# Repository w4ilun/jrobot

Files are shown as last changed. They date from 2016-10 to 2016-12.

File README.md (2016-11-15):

jrobot
A PLEN Robot Derivative designed at China . We love the PLEN2 robot but its expensive. This is our take on a lower cost version of the PLEN2 robot using 9g servo's.

The 3d printed parts are inspired by the PLEN2 parts but were redrawn from scratch to make use of the cheaper 9g servo motors.

Note: This is a work in progress. We are still busy building and testing it. Proceed at own risk :)

Please get kits [$120]
BUY KIT LINK
(https://item.taobao.com/item.htm?spm=a230r.1.14.28.0Gwvvy&id=531972040644&ns=1&abbucket=7#detail)

3d model: http://www.thingiverse.com/thing:1745439

qq group: 371582470

app: jrobot
ios(ios app store search jrobot) 
android:(http://sj.qq.com/myapp/detail.htm?apkName=jp.plen.scenography)

video demo:http://v.youku.com/v_show/id_XMTcwMTE4NjE5Mg==.html?from=y1.7-2

video app demo:https://youtu.be/BKA68jKV4QY

motion editor demo: https://youtu.be/AzxJYb-AGyE

3d printed jrobot

3d printed jrobot

3d printed jrobot

3d printed jrobot

3d printed jrobot

3d printed jrobot

3d printed jrobot

3d printed jrobot

3d printed jrobot

This software is released under the MIT License.

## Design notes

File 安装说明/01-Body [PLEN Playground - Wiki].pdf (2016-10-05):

2016/9/20 | Body [PLEN Playground Wiki]

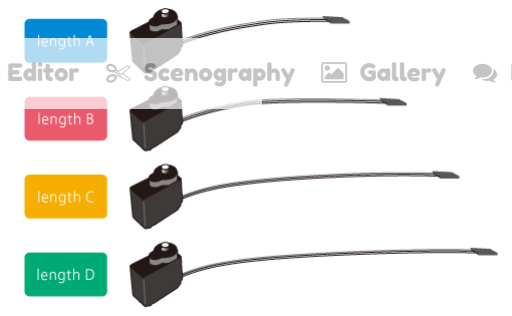
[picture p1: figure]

http://plen.jp/playground/wiki/tutorials/plen2/body | 1/3

# PLEN Playground - Wiki (http://plen.jp/playground/wiki/index.html)

# Body

## Table of Contents

1. Firmware Installation (http://plen.jp/playground/wiki/tutorials/plen2/firmware)
2. Connect a Battery (http://plen.jp/playground/wiki/tutorials/plen2/battery)
3. Arm (http://plen.jp/playground/wiki/tutorials/plen2/arm)
4. Leg (http://plen.jp/playground/wiki/tutorials/plen2/leg)
5. Head (http://plen.jp/playground/wiki/tutorials/plen2/head)
6. Body (http://plen.jp/playground/wiki/tutorials/plen2/body) Current section
7. Merge the Parts (http://plen.jp/playground/wiki/tutorials/plen2/merge)
8. Attach Covers (http://plen.jp/playground/wiki/tutorials/plen2/cover)
9. Tuning Up Home Positions (http://plen.jp/playground/wiki/tutorials/plen2/tune)

Prev < Head (http://plen.jp/playground/wiki/tutorials/plen2/head)
Next > Merge the Parts (http://plen.jp/playground/wiki/tutorials/plen2/merge)

## Parts List

Parts list of the body is enumerated below.

Name | Q'ty
body_middle.stl [https://github.com/plenprojectcompany/PLEN2/blob/master/stl/body_middle.stl] | 1
servo_bracket.stl [https://github.com/plenprojectcompany/PLEN2/blob/master/stl/servo_bracket.stl] | 2
servo_bracket_mirror.stl [https://github.com/plenprojectcompany/PLEN2/blob/master/stl/servo_bracket_mirror.stl] | 2
servo_fixer.stl [https://github.com/plenprojectcompany/PLEN2/blob/master/stl/servo_fixer.stl] | 1
Servo Motor (Length A) | 2
Servo Motor (Length B) | 2
Low Head Screw | 4
Screw | 2
Finished Head (http://plen.jp/playground/wiki/tutorials/plen2/head) | 1
Control Board with Power Supply (http://plen.jp/playground/wiki/tutorials/plen2/battery) | 1

## Print Detail

Body (http://plen.jp/playground/wiki/specifications/print_detail/body)

## Assembling Process

### Parts List

### Attach Servos

- Home (http://plen.jp/playground/) Motion Editor (http://plen.jp/playground/motion-editor/) Scenography (http://plen.jp/playground/scenography/) Gallery (http://plen.jp/playground/gallery/) Forum (http://plen.jp/playground/forum/) Wiki (http://plen.jp/playground/wiki/)

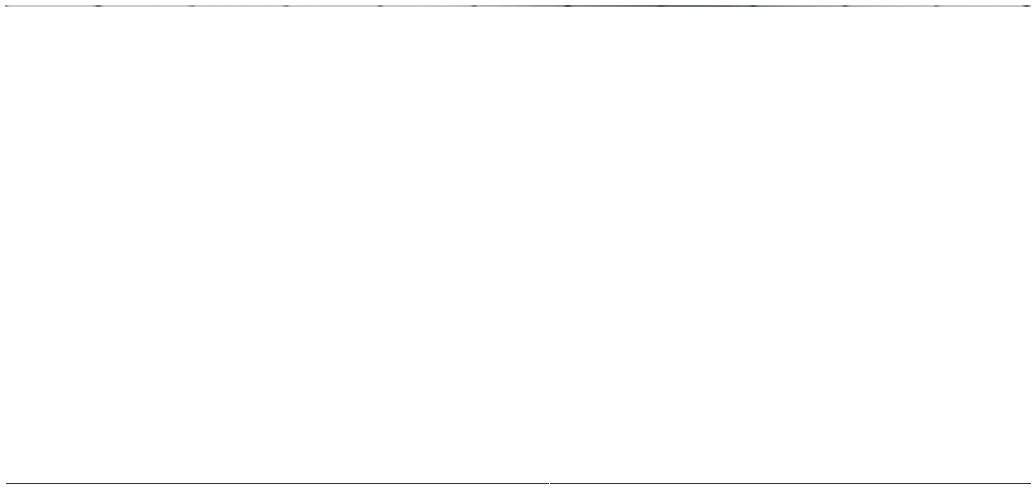
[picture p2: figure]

Attention!: Servos' cables are passed through inside the body's gap.

### Attach the Finished Head

Attention!: Head-board's cable is passed through inside the body's gap.

### Attach Spacer for Servos

### Attach the Control Board

Attention!: Control-board's cable is passed through inside the body's gap.

Attention!: Please use normal screws to attach the control-board.

### Attach the Brackets

Attention!: Before to attach the brackets, you should connect servos' cables and the control-board. When it was completed, please turn on both switches and keep the status.

Attention!: Please connect the white wire which is owned by a servo to inside of the control-board.

Attention!: Attach a servo-bracket to the body. At that time, please check it is placed approximately parallel to edge of the body.

Attention!: Attach a servo-bracket (mirror) to the body. At that time, please check it is placed approximately parallel to edge of the body.

Attention!: Attach a servo-bracket to the body. At that time, please check it is placed approximately parallel to edge of the body.

Attention!: Attach a servo-bracket (mirror) to the body. At that time, please check it is placed approximately parallel to edge of the body.

### Finished Body

Prev < Head (http://plen.jp/playground/wiki/tutorials/plen2/head)
Next > Merge the Parts (http://plen.jp/playground/wiki/tutorials/plen2/merge)

tutorials/plen2/body.txt · Last modified: 2016/04/21 19:39 (external edit)

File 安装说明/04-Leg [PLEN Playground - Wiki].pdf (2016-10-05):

2016/9/20 | Leg [PLEN Playground Wiki]

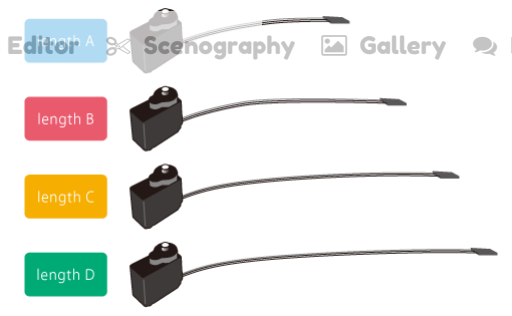
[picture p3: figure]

http://plen.jp/playground/wiki/tutorials/plen2/leg | 1/6

# PLEN Playground - Wiki (http://plen.jp/playground/wiki/index.html)

# Leg

## Table of Contents

1. Firmware Installation (http://plen.jp/playground/wiki/tutorials/plen2/firmware)
2. Connect a Battery (http://plen.jp/playground/wiki/tutorials/plen2/battery)
3. Arm (http://plen.jp/playground/wiki/tutorials/plen2/arm)
4. Leg (http://plen.jp/playground/wiki/tutorials/plen2/leg) Current section
5. Head (http://plen.jp/playground/wiki/tutorials/plen2/head)
6. Body (http://plen.jp/playground/wiki/tutorials/plen2/body)
7. Merge the Parts (http://plen.jp/playground/wiki/tutorials/plen2/merge)
8. Attach Covers (http://plen.jp/playground/wiki/tutorials/plen2/cover)
9. Tuning Up Home Positions (http://plen.jp/playground/wiki/tutorials/plen2/tune)

Prev < Arm (http://plen.jp/playground/wiki/tutorials/plen2/arm)
Next > Head (http://plen.jp/playground/wiki/tutorials/plen2/head)

## Parts List

Parts list of the left leg is enumerated below. If you would like to assemble the right leg, please use parts which have '_mirror' suffix or no suffix.

Name | Q'ty
serve_horn.stl [https://github.com/plenprojectcompany/PLEN2/blob/master/stl/servo_horn.stl] | 4
servo_assem_type2.stl [https://github.com/plenprojectcompany/PLEN2/blob/master/stl/servo_assem_type2.stl] | 1
servo_assem_type2_mirror.stl [https://github.com/plenprojectcompany/PLEN2/blob/master/stl/servo_assem_type2_mirror.stl] | 1
servo_bracket_knee_mirror.stl [https://github.com/plenprojectcompany/PLEN2/blob/master/stl/servo_bracket_knee_mirror.stl] | 1
servo_bracket_shin_mirror.stl [https://github.com/plenprojectcompany/PLEN2/blob/master/stl/servo_bracket_shin_mirror.stl] | 1
servo_bracket_ankle_1_mirror.stl [https://github.com/plenprojectcompany/PLEN2/blob/master/stl/servo_bracket_ankle_1_mirror.stl] | 1
servo_bracket_ankle_2_mirror.stl [https://github.com/plenprojectcompany/PLEN2/blob/master/stl/servo_bracket_ankle_2_mirror.stl] | 1
foot_mirror.stl [https://github.com/plenprojectcompany/PLEN2/blob/master/stl/foot_mirror.stl] | 1
Servo Motor (Length B) | 2
Servo Motor (Length C) | 1
Servo Motor (Length D) | 2

## Print Detail

Leg x2 (http://plen.jp/playground/wiki/specifications/print_detail/legs)

## Assembling Process

### Parts List

- Home Motion Editor Scenography Gallery (http://plen.jp/playground/wiki/_media/tutorials/plen2/motors.png) Forum (http://plen.jp/playground/forum/) Wiki (http://plen.jp/playground/wiki/_media/tutorials/plen2/motors.png)

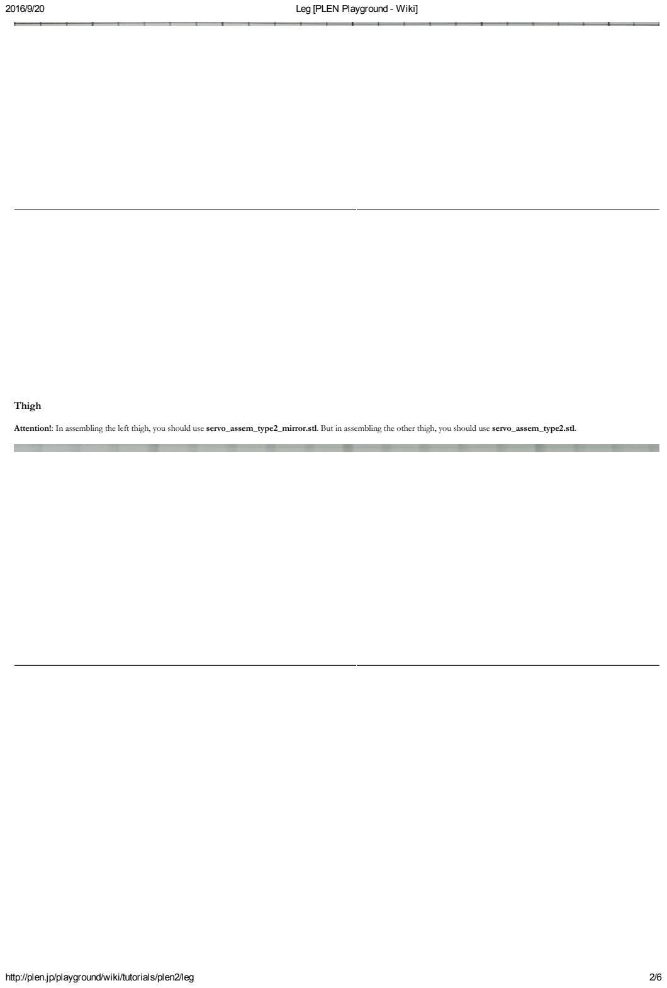
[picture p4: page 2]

### Thigh

Attention!: In assembling the left thigh, you should use servo_assem_type2_mirror.stl. But in assembling the other thigh, you should use servo_assem_type2.stl.

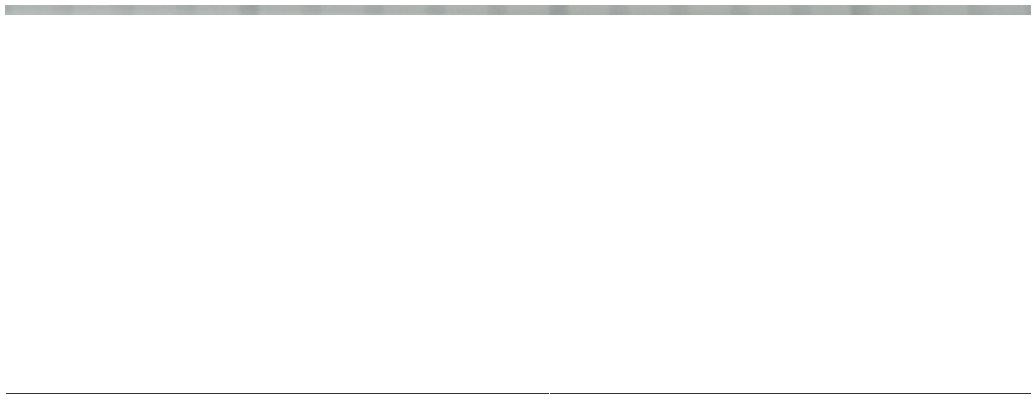
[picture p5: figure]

### Knee

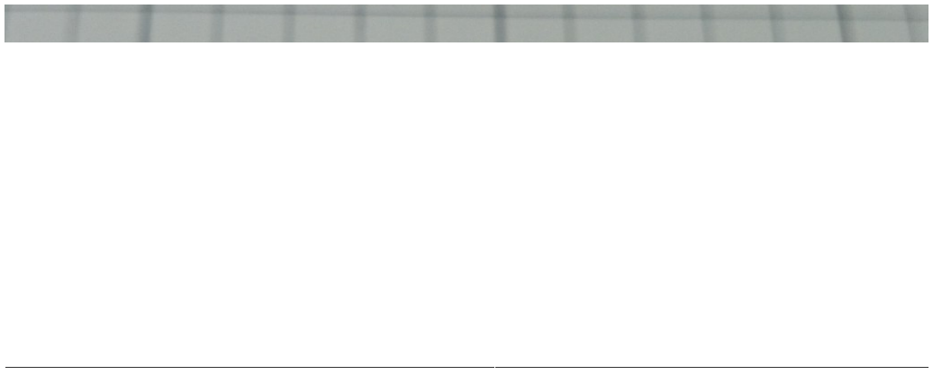
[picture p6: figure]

### Upper Foot

Attention!: In assembling the left upper foot, you should use servo_assem_type2.stl. But in assembling the other upper foot, you should use servo_assem_type2_mirror.stl.

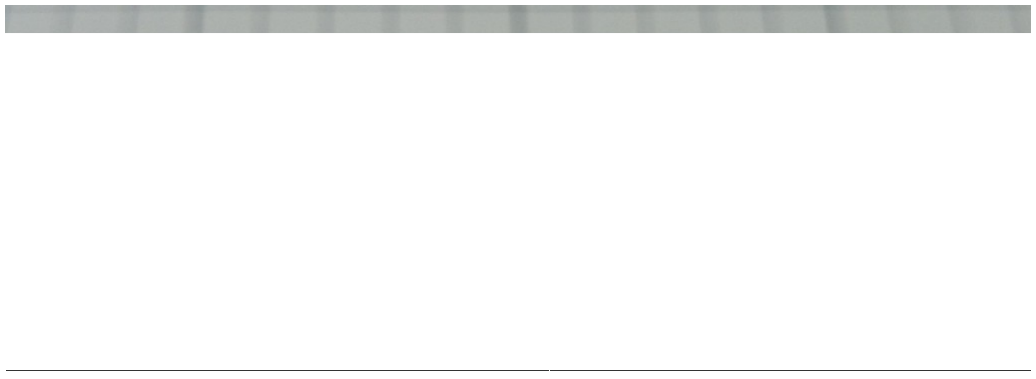
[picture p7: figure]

### Lower Foot

Attention!: If you assemble plastic cast parts, this step has already been completed.

### Merge Parts

Attention!: Before to merge the parts, you should connect servos' cables and the control-board. When it was completed, please turn on both switches and keep the status.

Attention!: Please connect the white wire which is owned by a servo to inside of the control-board.

Attention!: Attach a servo-horn to the left thigh. At that time, please check it is placed approximately parallel to edge of the servo.

Attention!: Attach a servo-horn to the left knee. At that time, please check it is placed approximately parallel to edge of the servo.

Attention!: Attach a servo-horn to the left upper foot. At that time, please check it is placed approximately parallel to edge of the servo.

Attention!: In merging the left shin and the left upper foot, servos' cables are passed through inside the left shin.

Attention!: Attach a servo-horn to the left upper foot. At that time, please check it is placed approximately parallel to edge of the servo.

### Finished Leg

Prev < Arm (http://plen.jp/playground/wiki/tutorials/plen2/arm)
Next > Head (http://plen.jp/playground/wiki/tutorials/plen2/head)

tutorials/plen2/leg.txt · Last modified: 2016/04/21 19:38 (external edit)

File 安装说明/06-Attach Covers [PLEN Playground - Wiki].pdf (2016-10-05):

2016/9/20 | Attach Covers [PLEN Playground Wiki]
http://plen.jp/playground/wiki/tutorials/plen2/cover | 1/7

## PLEN Playground - Wiki (http://plen.jp/playground/wiki/index.html)

# Attach Covers

## Table of Contents

1. Firmware Installation (http://plen.jp/playground/wiki/tutorials/plen2/firmware)
2. Connect a Battery (http://plen.jp/playground/wiki/tutorials/plen2/battery)
3. Arm (http://plen.jp/playground/wiki/tutorials/plen2/arm)
4. Leg (http://plen.jp/playground/wiki/tutorials/plen2/leg)
5. Head (http://plen.jp/playground/wiki/tutorials/plen2/head)
6. Body (http://plen.jp/playground/wiki/tutorials/plen2/body)
7. Merge the Parts (http://plen.jp/playground/wiki/tutorials/plen2/merge)
8. Attach Covers (http://plen.jp/playground/wiki/tutorials/plen2/cover) Current section
9. Tuning Up Home Positions (http://plen.jp/playground/wiki/tutorials/plen2/tune)

Prev < Merge the Parts (http://plen.jp/playground/wiki/tutorials/plen2/merge)
Next > Tuning Up Home Positions (http://plen.jp/playground/wiki/tutorials/plen2/tune)

## Parts List

Parts list of the covers is enumerated below.

Name | Q'ty
body_front.stl [https://github.com/plenprojectcompany/PLEN2/blob/master/stl/body_front.stl] | 1
body_rear.stl [https://github.com/plenprojectcompany/PLEN2/blob/master/stl/body_rear.stl] | 1
power_switch_holder.stl [https://github.com/plenprojectcompany/PLEN2/blob/master/stl/power_switch_holder.stl] | 1
Finished To Merge PLEN2 (http://plen.jp/playground/wiki/tutorials/plen2/merge) | 1

## Print Detail

Body (http://plen.jp/playground/wiki/specifications/print_detail/body)

## Assembling Process

Parts List

- Home (http://plen.jp/playground/) Motion Editor (http://plen.jp/playground/motion-editor/) Scenography (http://plen.jp/playground/scenography/) Gallery (http://plen.jp/playground/gallery/) Forum (http://plen.jp/playground/forum/) Wiki (http://plen.jp/playground/wiki/)

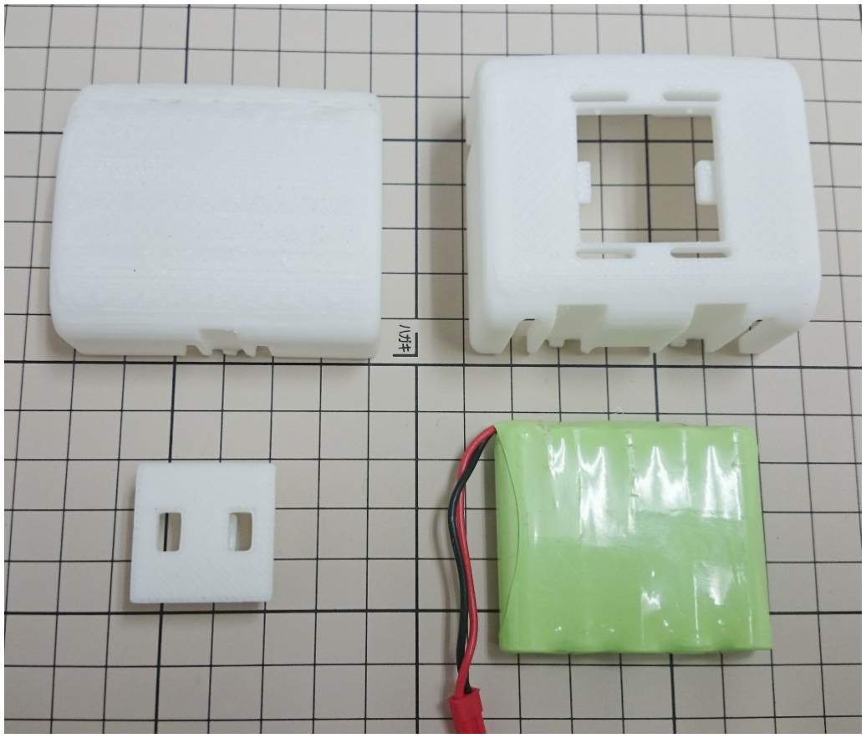
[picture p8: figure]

Attach Switch Holder

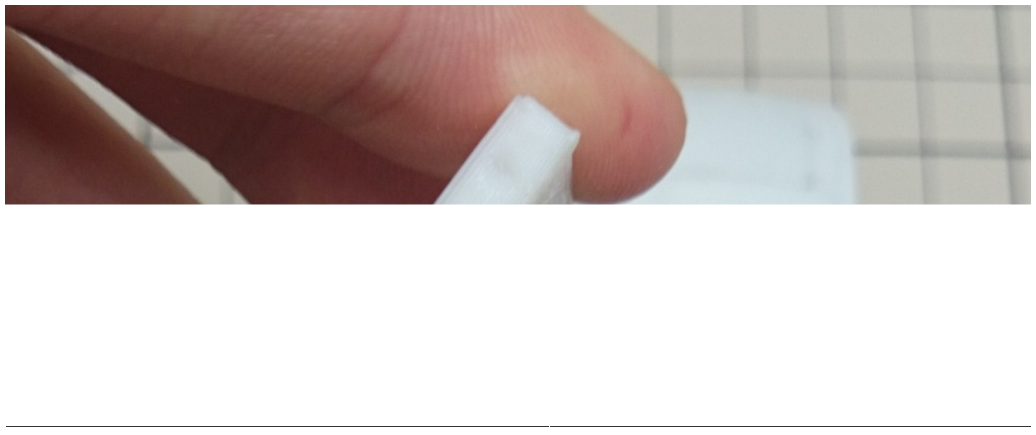
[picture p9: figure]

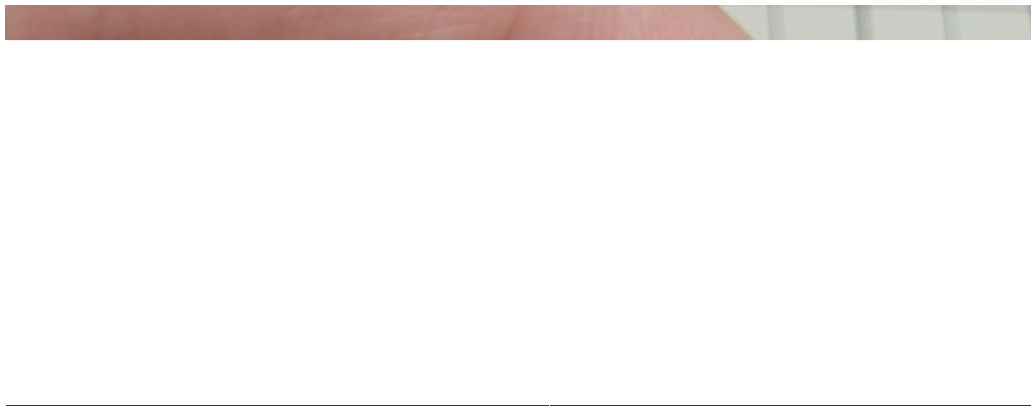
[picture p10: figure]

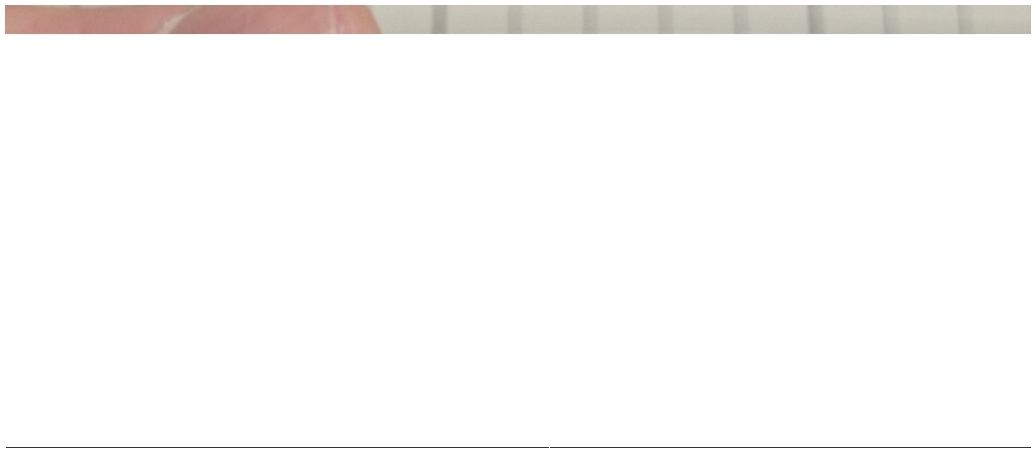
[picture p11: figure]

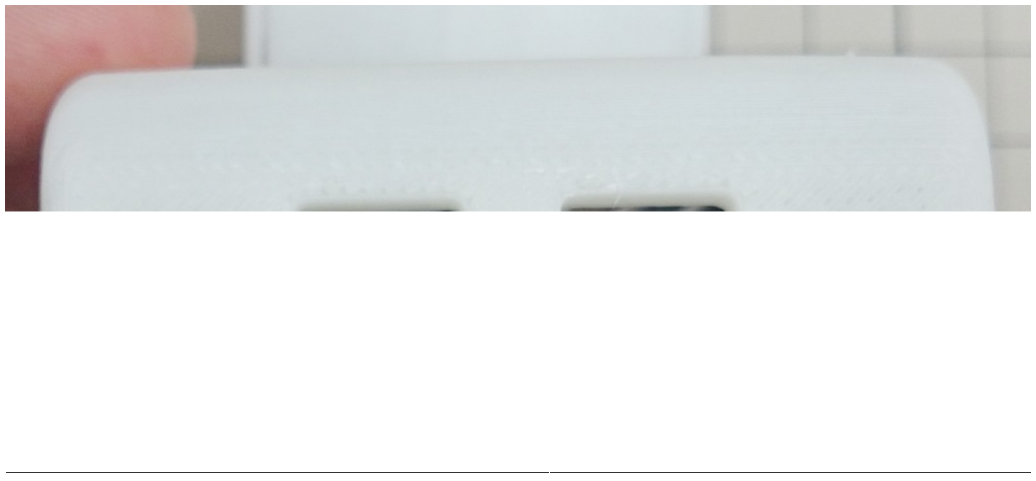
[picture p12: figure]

Attach Back Cover

Attention!: Please bundle servos' cables and fit the gap on the back.

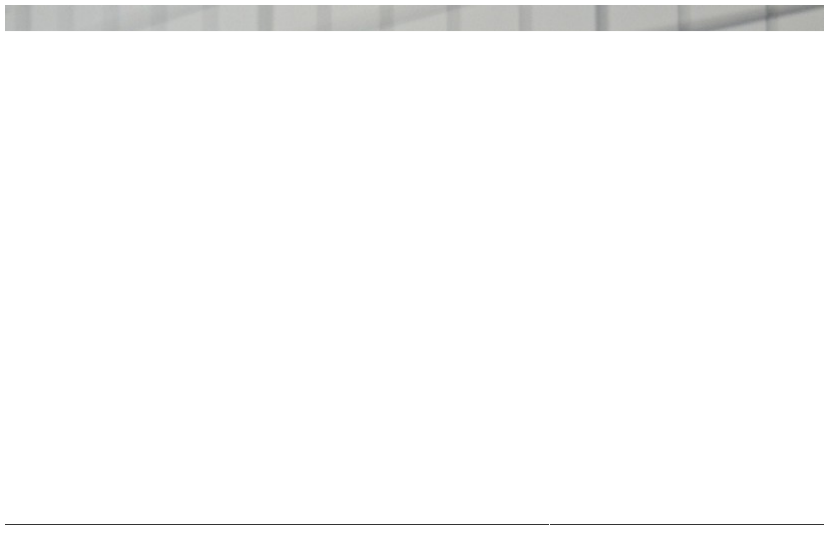
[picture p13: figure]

Attach Chest Cover

Attention!: Please fit the battery's cables gap inside the chest.

Finished PLEN2

Prev < Merge the Parts (http://plen.jp/playground/wiki/tutorials/plen2/merge)
Next > Tuning Up Home Positions (http://plen.jp/playground/wiki/tutorials/plen2/tune)

tutorials/plen2/cover.txt · Last modified: 2016/04/21 19:39 (external edit)

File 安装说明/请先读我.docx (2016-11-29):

1. 注意点：
    i. 关于电池：出厂锂电处于不饱和状态(不知道有多少电)，请先给电池充满电(充电器灯的状态会从红色->橙色->绿色，绿色时表示电池已经完全充满),电池接到电池连接线的时候，请务必保证红色线对红色线，黑色线对黑色线,每个电池有两组线(一组用来充电，一组用来放电，随意选一组，这样是为了可以不用拆plen2前胸就能充电)
    ii. 在使用机器人的过程中，如果发现机器人的眼睛灭了，即表示电池电量即将不足，请及时充电。
  b) 关于app：可以在IOS应用市场或在Android二个应用市场 (应用宝| 豌豆荚)搜索jrobot下载。请阅读app左侧菜单栏的帮助和反馈，了解如何配置网络和连接机器人。
  c) 关于app中的网络配置：
    i. 一键配置到室内wifi：

请在配置前先关闭Robot电源，然后再SSID和密码端填入家里使用的路由器的SSID和密码(务必确保这两项正确，否则配置会失败)，然后打开Robot电源，此时要立刻点击APP中的配置按钮,等待30秒左右，Android客户端会返回配置结果，IOS的暂时无返回结果的对话框，可以手动点击退出配置，然后进入设备扫描页面扫描机器人，若配置成功此处能扫描到机器人。

    ii. 无wifi情况下

打开机器人电源，等待30秒后，Robot会退出接受网络配置状态，进入创建自主热点模式，此时可以使用手机在Wifi界面搜索Robot的热点( SSID:Jrobot*****,密码为12345678xyz)，接着在扫描设备界面扫描到机器人并连接后就可以用APP控制Robot了。

  d) 关于舵机回中，PLEN2的仿人形结构和舵机的转动角度范围(<180度)限制每个舵机的初始角度不能是90度，而且每个关节的初始角度不一定一样，切记切记！！！

所以在安装关节的时候，请务必如下操作：

1.关闭主板电源

2.先把舵机插到主板上对应这个关节的舵机插槽

3.打开主板电源，舵机自动转到对应关节的初始位置。

4.关闭主板电源，安装关节。

5.打开主板电源，连上APP，在APP中的开发者模式->回中，将对应的关节微调，调正，然后点回中界面左侧的回中将调整后的回中角度保存到Robot

e) 关于舵机及摆臂和轴承的处理：

1.每个舵机的两个耳朵都需要剪去，尽量剪平，另外把舵机上的贴纸都撕去

2.小轴承用于虚轴处，固定在打印件上，塞进去后，压平即可。

3.舵机摆臂用到了2中，一种是半一字的摆臂，用在腿各个关节和手关节，只需要将摆臂末端稍微剪短后放入打印件用胶水固定(也可以关节安装完后再用胶水稍微固定下，前者刚性好，难安装，后者好安装，刚性略差);另外一种摆臂是圆形，用在肩关节和大腿根关节，用胶水固定后，重物压着，牢固后即可以安装。

f) 关于板子：

1.主板固件已经刷好，动作文件均已经下载好，直接用即可(除非要对固件进行修改，并且对这一块很熟悉，否则不推荐自己更新固件)

2.头板和主板的3pin的连接线可以通过把接插件竖直的方式放入头部(横着放不进)

2. 关于安装，

1.安装顺序，先胸部四个舵机，电池，头，头板，主板，双手并安装到身体上(及时对手部以及大腿根舵机进行微调进入双手自然放下的立正姿势)，双腿(及时对腿部舵机进行微调进入双手自然放下的立正姿势)，双腿安装到身体上

2.可以看该目录下各部位的安装说明pdf，也可以参照plen2官网的安装说明(本套3D模型是在PLEN2的模型上进行了修改，主要是解决舵机摆臂的问题，无需使用官方的注塑件，只需要使用舵机自己带的摆臂即可，其余安装方式和原版一致)http://plen.jp/playground/wiki/tutorials/index.html

3. 接线图(如果看不清楚标号，可以看同级目录下的接线图.png,因为做了一些升级，舵机的接线序号和原版的有些差别，以本图为准，另外无需看主板上的丝印)：

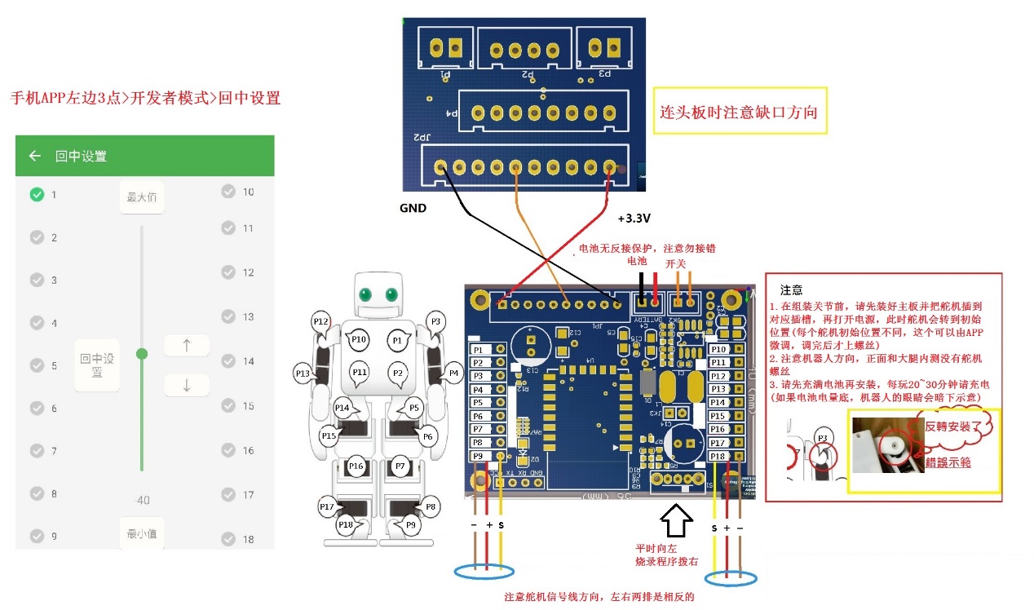
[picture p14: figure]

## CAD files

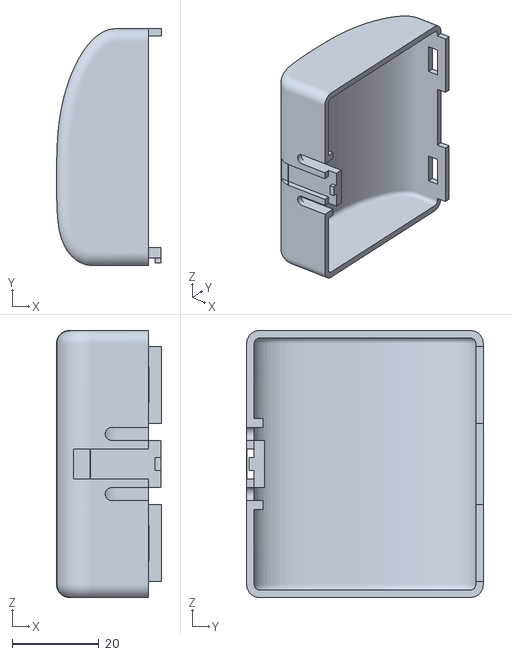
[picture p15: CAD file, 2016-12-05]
stl/body/body_front.STL
24.2 x 54.6 x 61.6

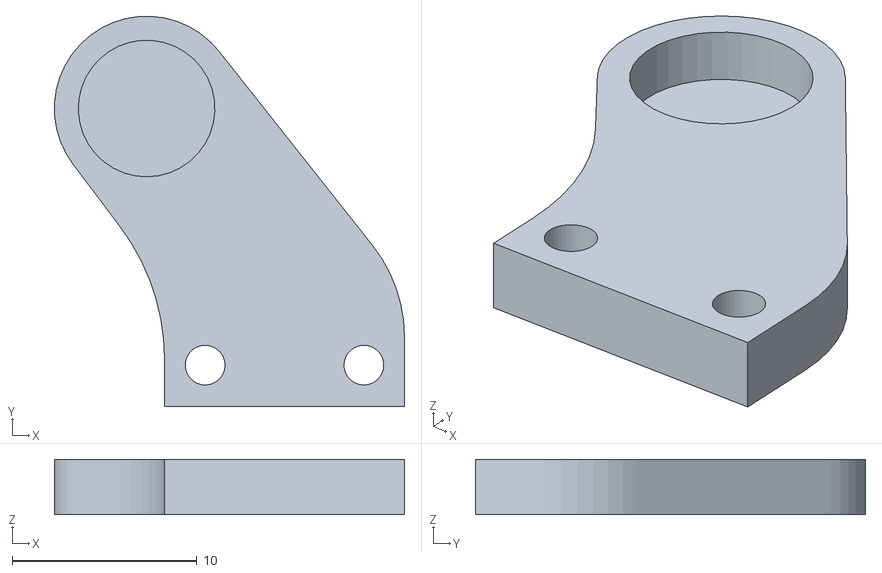
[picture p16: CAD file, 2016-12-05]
stl/body/servo_type/servo_bracket_part1_mirror.STL
19.0 x 21.1 x 3.00

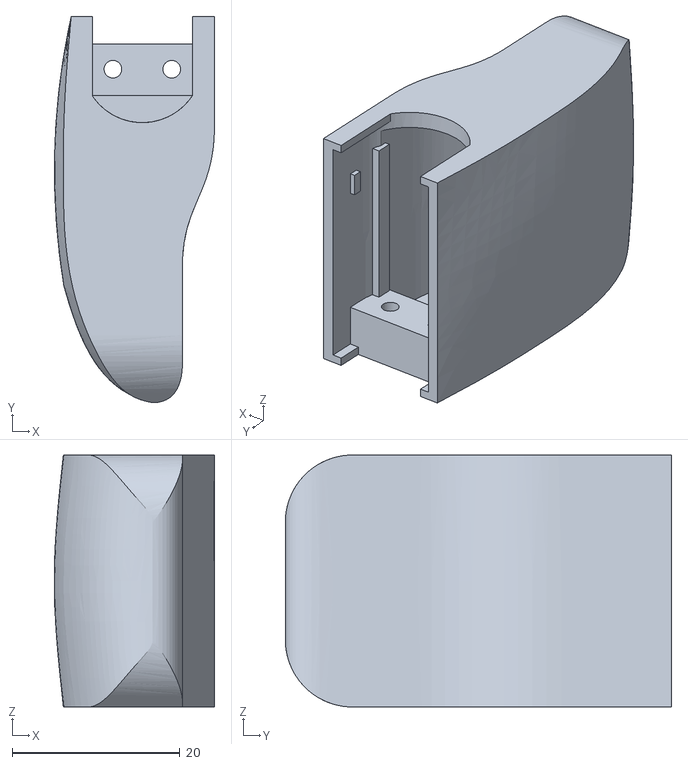
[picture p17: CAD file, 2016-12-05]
stl/hand/hand_mirror.STL
19.1 x 46.0 x 30.0

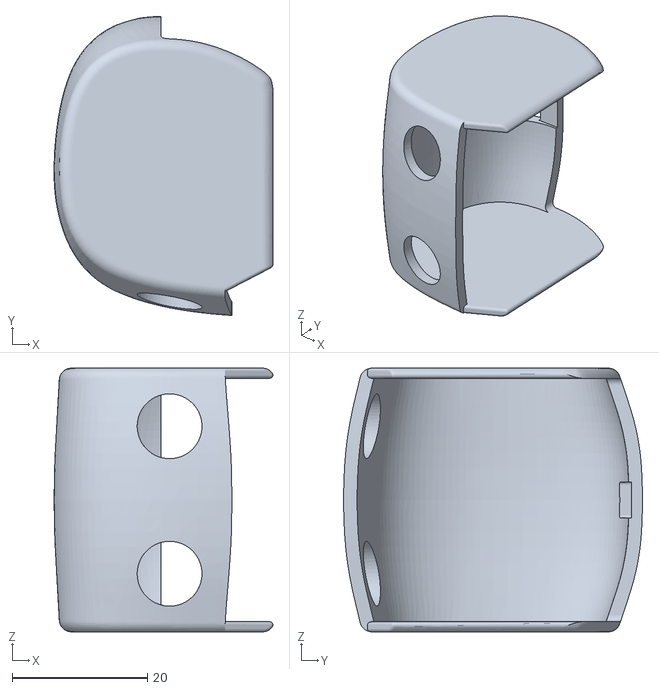
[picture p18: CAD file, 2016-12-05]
stl/head/HEAD.STL
32.4 x 44.3 x 39.0

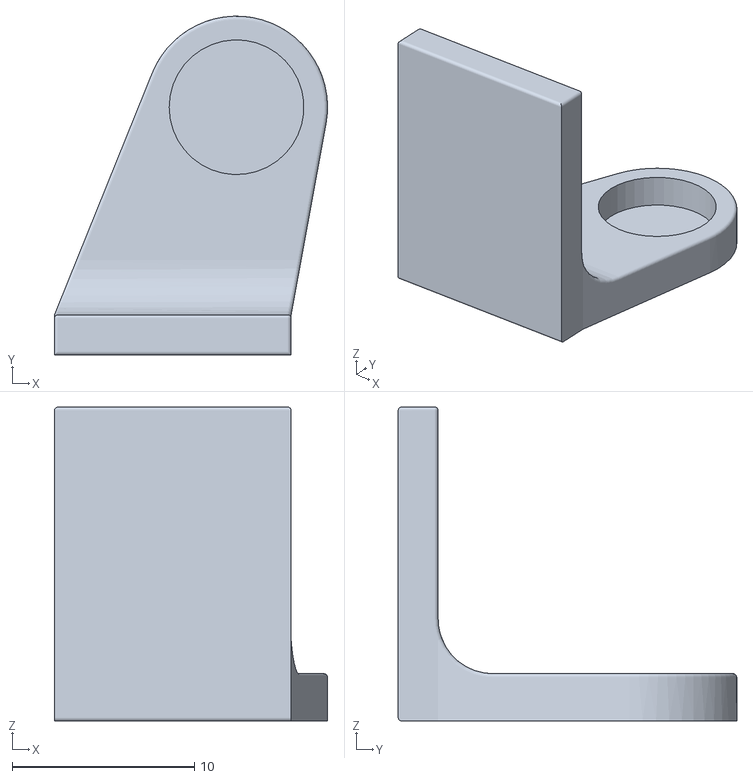
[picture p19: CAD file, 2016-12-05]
stl/leg/foot/servo_bracket_ankle_2_mirror.STL
15.0 x 18.6 x 17.2

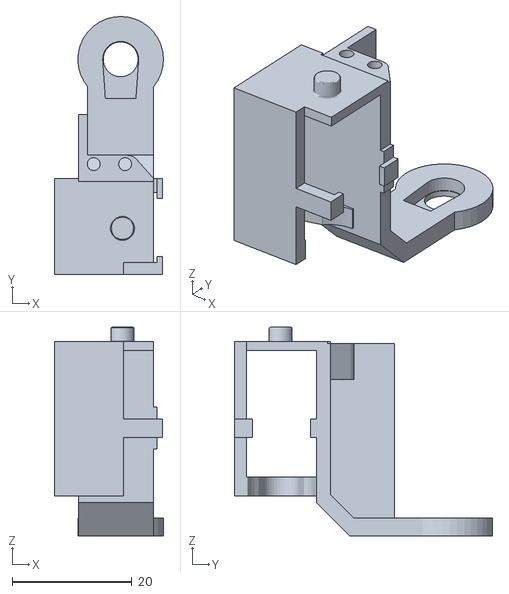
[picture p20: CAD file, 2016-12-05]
stl/leg/knee/servo_bracket_knee.STL
18.2 x 43.0 x 34.8

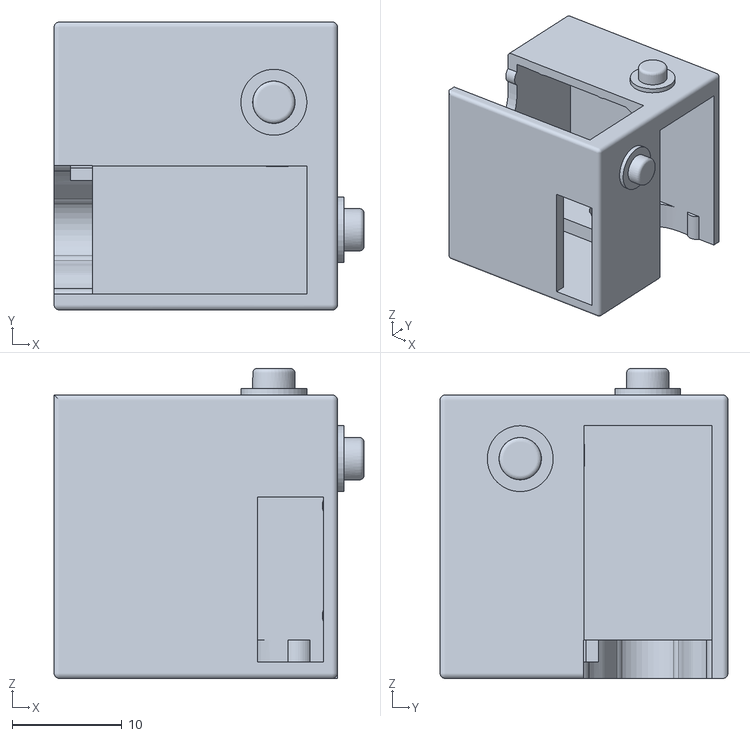
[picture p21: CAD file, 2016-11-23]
stl/leg/servo_assem_type2.STL
28.2 x 26.2 x 28.2

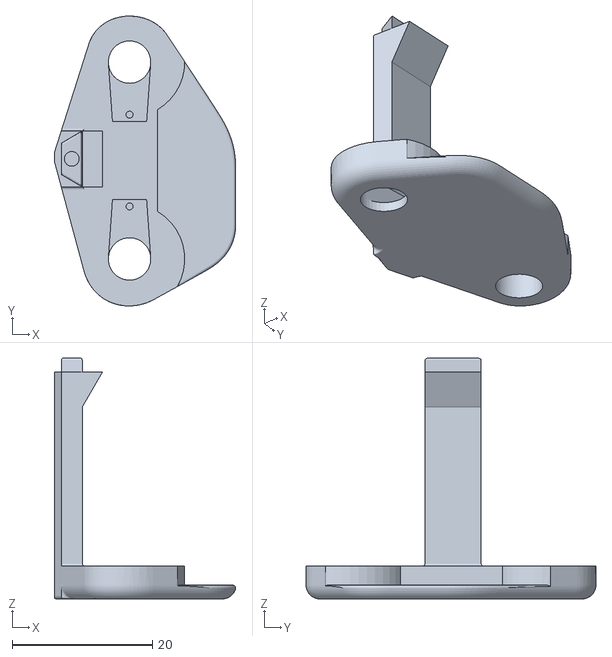
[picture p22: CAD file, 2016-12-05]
stl/leg/shin/servo_bracket_shin_part1.STL
25.9 x 41.4 x 34.4

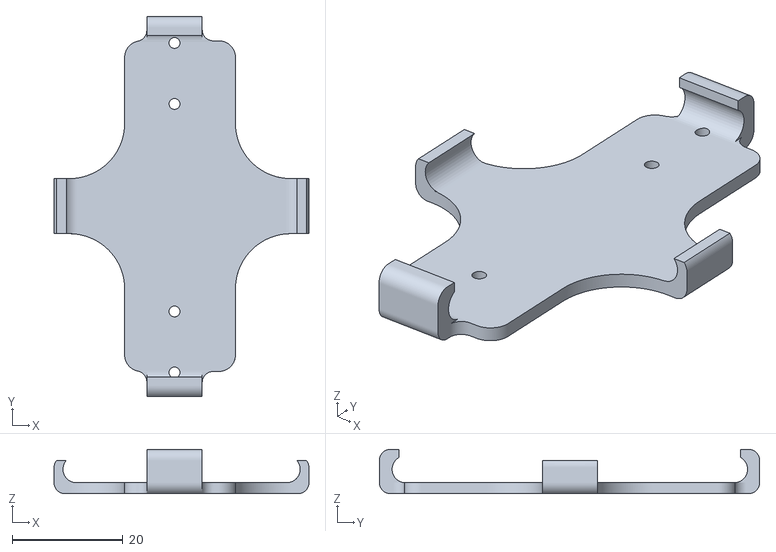
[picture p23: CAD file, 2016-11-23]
stl/toys/skate_base.stl
46.0 x 68.6 x 8.00

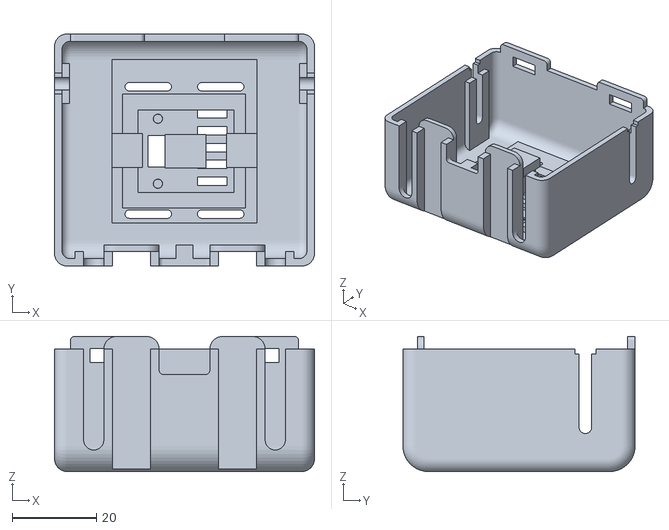
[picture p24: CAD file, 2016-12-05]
stl/body/body_rear_op.STL
61.6 x 55.0 x 32.0

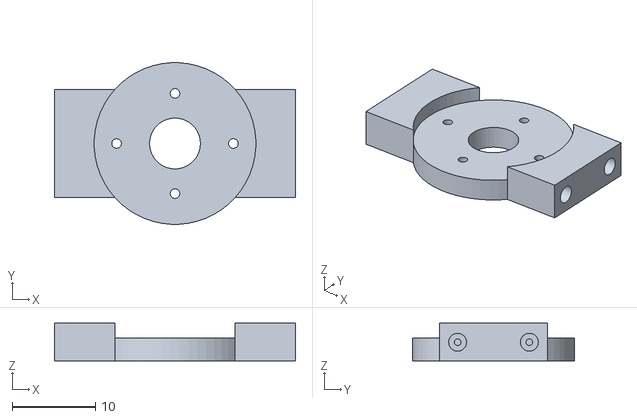
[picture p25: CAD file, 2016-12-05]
stl/body/servo_type/servo_bracket_part2.STL
28.9 x 19.4 x 4.55

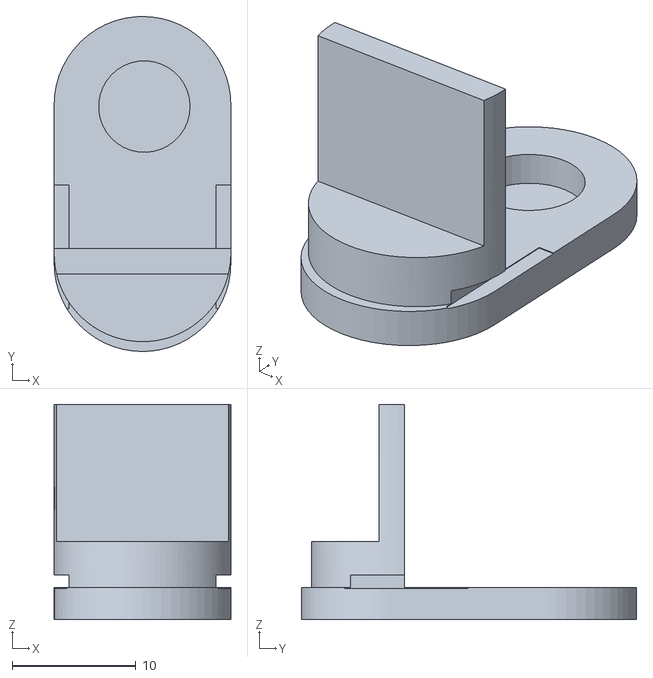
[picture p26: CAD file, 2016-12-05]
stl/hand/servo_bracket_elbow_2.STL
14.3 x 27.1 x 17.4

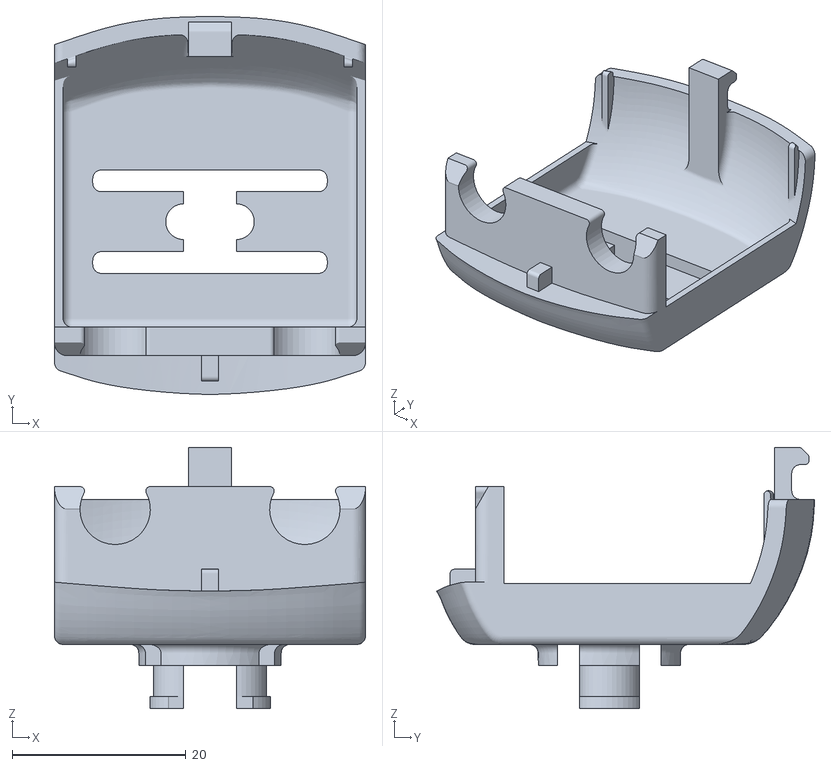
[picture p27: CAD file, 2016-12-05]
stl/head/BARB.STL
35.8 x 43.5 x 30.1

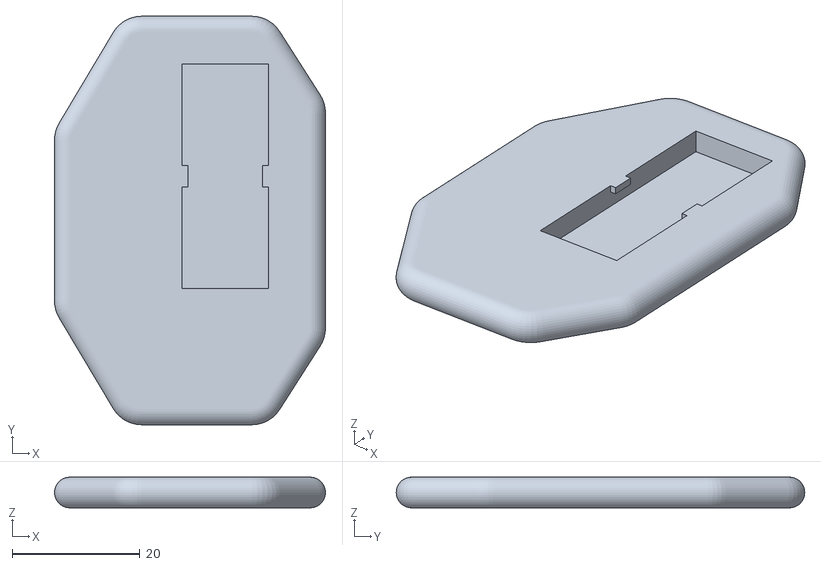
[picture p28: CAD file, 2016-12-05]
stl/leg/foot/foot.STL
42.4 x 63.9 x 4.80

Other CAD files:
stl/leg/knee/servo_bracket_knee_mirror.STL
stl/leg/servo_assem_type2_mirror.STL
stl/leg/shin/servo_bracket_shin_part2_mirror.STL
stl/toys/skate_wheel_seats.stl
stl/body/body_middle.STL
stl/body/servo_fixer.stl
stl/body/servo_type/servo_bracket__part3_mirror.STL
stl/body/servo_type/servo_bracket_part1.STL
stl/body/servo_type/servo_bracket_part3.STL
stl/hand/hand.STL
stl/hand/servo_assem_type1.STL
stl/hand/servo_bracket_elbow_1.STL
stl/leg/foot/foot_mirror.STL
stl/leg/foot/servo_bracket_ankle_1.STL
stl/leg/foot/servo_bracket_ankle_1_mirror.STL
stl/leg/foot/servo_bracket_ankle_2.STL
stl/leg/knee/servo_bracket_knee_part1.STL
stl/leg/knee/servo_bracket_knee_part1_mirror.STL
stl/leg/shin/servo_bracket_shin_part1_mirror.STL
stl/leg/shin/servo_bracket_shin_part2.STL

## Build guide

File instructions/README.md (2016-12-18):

##Before you begin

* Battery
	1. Please first fully charge the battery pack. The battery charger indicator light will turn from red to orange to green when fully charged. Ensure the polarity is correct when connecting the battery to the charger. Each battery pack has two sets of wires/connectors, one is for connecting and powering the robot, the other is for charging the battery.

	2. During operation, the robot's LED eyes will turn off when the battery level is too low. Please recharge the battery at that time.

* App
	1. You can find the app for by searching for "jrobot" in the app store for iOS, and on [](http://sj.qq.com/myapp/) for Android.
	2. The side menu of the app contains additional help information and settings.

* Network Settings
	1. First switch off the power on the robot, then enter your home netowrk's WiFi SSID and password (by pressing the + icon on the top right). Switch on the robot and immediately press the "config" button, then wait 30 seconds. Upon connecting, Android users will see connection results, while iOS users will not, and require to manually return to settings view. You ca then return to the main view to scan for your robot and establish the connection.
	2. If you do not have a home WiFi network, switch on the robot and wait for 30 seconds. The robot will leave connection mode and create it's own WiFi hotspot. You can then connect to the robot's WiFi hotspot with your phone (SSID: Jrobot***** Password: 12345678xyz). Once WiFi is connected, you can then scan for your robot and connect to it.

* Servo Centering
	1. The servos have a range of < 180 degrees and they are not always centered to 90 degrees out of the box. Every robot joint's starting angle is not the same either **you must first center all the servos before assembly!**
		1. Switch off the board
		2. Connect every servo according to their joint number
		3. Switch on the board, the servos will automatically align to their starting position
		4. Switch off the board, and begin assembling your robot's joints
		5. Switch on the board and connect with the app, on the side menu, enter "Developer mode" => "Home position" to fine tune the joint servo positions. Once tuned, remember to press the "Home position" button to save your settings.

* Servo Preparation
	1. Each servo has two mounting tabs on its side. Remove them and ensure the sides are as flat as possible. Remove all the stickers.
	2. The joint servos are anchored to the 3D printed parts with the servo horns and bearings. Push them flat into positon and secure the servos.

* Main Board
	1. The firmware has already been flashed and updated on the board, including the animation settings. It is ready to use out of the box. Please do not manually update the firmware unless you are familiar with the firmware code and have made changes.
	2. The 3 pin connector to the head board can inserted vertically (it will not fit horizontally)

* Assembly
	1. Order of assembly
		1. Chest (4 servos)
		2. Battery pack
		3. Head
		4. Head board
		5. Main board
		6. Arms (attached to body). At this time, also fine tune the servo positions so the arms are hanging narturally beside the body
		7. Legs. At this time, also fine tune the servo positions so the robot is standing in a natural upright position
	2. Refer to the assembly instructions pdf for further details, or reference the official Plen2 robot's assembly instructions [](http://plen.jp/playground/wiki/tutorials/index.html)

* Connection Diagram
	1. Please refer to this diagram for the pin connections and servo/joint numbering. You can ignore the board's silkscreen printings as the numbering may have changed.

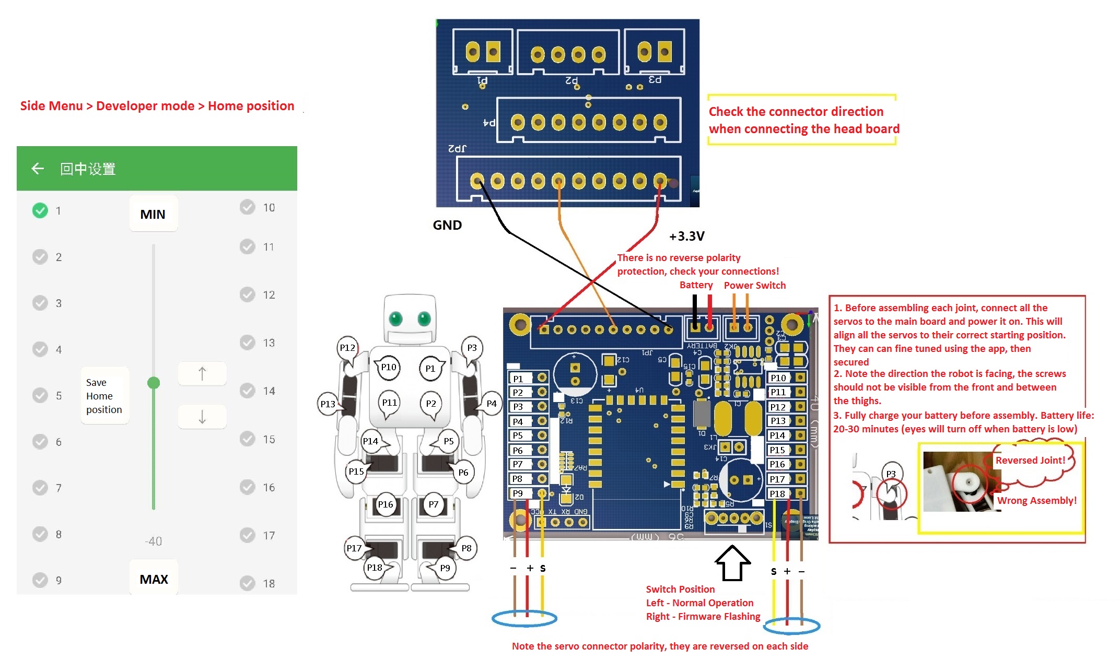
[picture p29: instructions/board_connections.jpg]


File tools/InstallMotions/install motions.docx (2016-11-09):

1、 打开MotionInstaller-PL2302.exe或者MotionInstaller-ch340.exe(如果是买套件自带的请选PL2302否则请选后者)

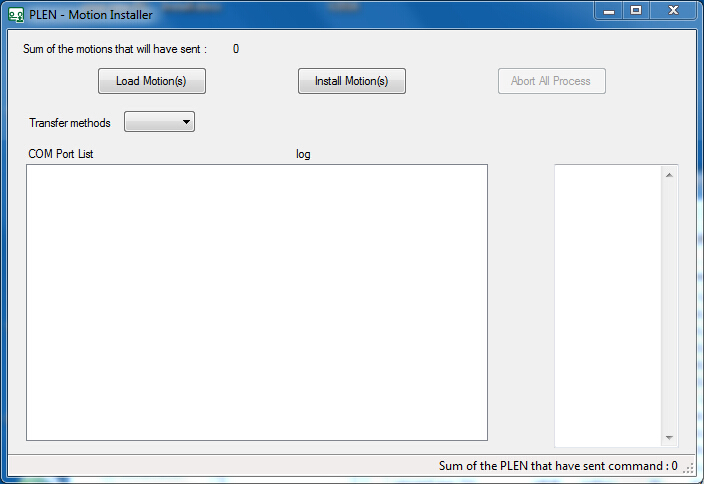
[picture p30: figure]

2、 将USB转串口连接到机器人主板

将机器人断电，机器人的串口在左下角 从左到右依次为VCC,TX,RX,GND(如下图) 分别接USB转串口的+3.3V(不可以接5V，会烧板子的),RX,TX, GND,

即

机器人 <-> usb转串口

VCC <-> +3.3V

TX <-> RX

RX <-> TX

GND <-> GND

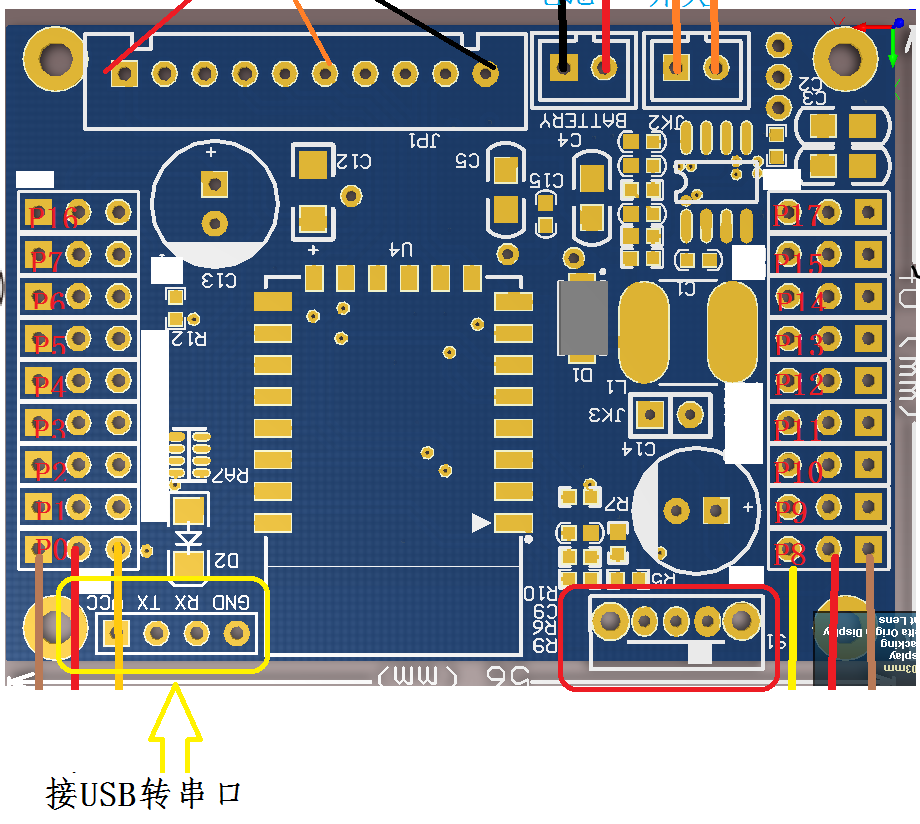
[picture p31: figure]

3、 install motions

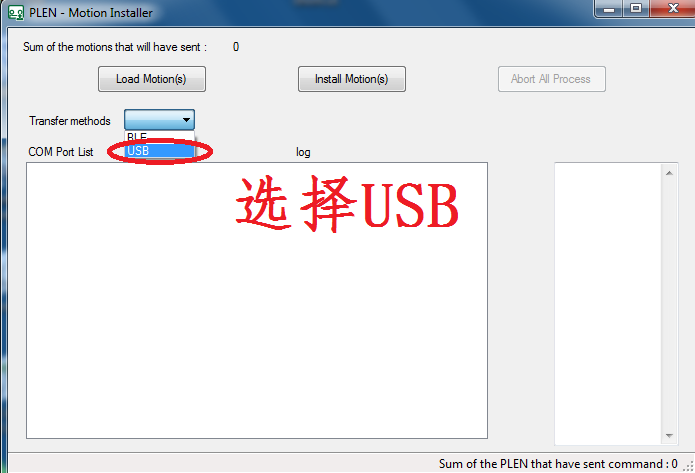
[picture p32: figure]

然后再Com Post List里左键单击你的USB转串口号(如果此处无串口号，请去我的电脑->设备管理器里查看，如果usb转串口没有安装驱动，请度娘PL2303驱动安装)

之后点击Load Motions把当前同级目录下的所有动作都选进去后，点击Install motions，然后等待右侧安装完毕即可。

注意机器人电源开关全程关闭

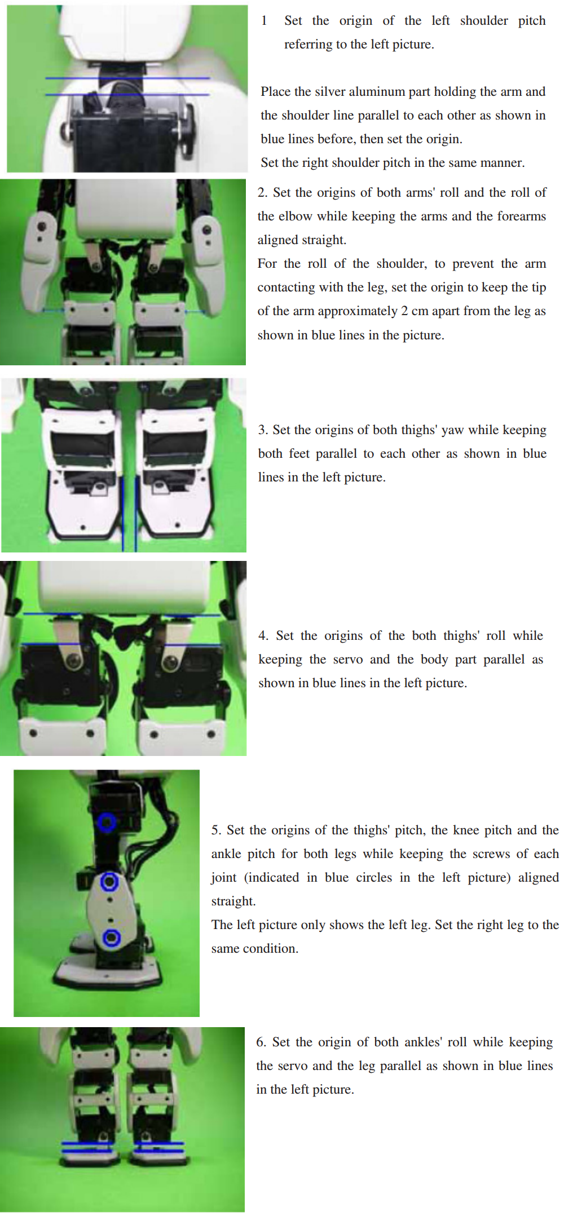
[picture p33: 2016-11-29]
instructions/cal_steps.png

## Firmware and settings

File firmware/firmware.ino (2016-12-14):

/*
  Copyright (c) 2015,
  - Kazuyuki TAKASE - https://github.com/junbowu
  - PLEN Project Company Inc. - https://plen.jp

  This software is released under the MIT License.
  (See also : http://opensource.org/licenses/mit-license.php)
*/

#include <string.h>

#include <Wire.h>
#include <Servo.h>

#include "JointController.h"
#include "Motion.h"
#include "MotionController.h"
#include "Interpreter.h"
#include "Pin.h"
#include "Parser.h"
#include "Protocol.h"
#include "System.h"
#include "Profiler.h"
#include "ExternalFs.h"

#if ENSOUL_PLEN2
#include "AccelerationGyroSensor.h"
#include "Soul.h"
#endif

unsigned char ssid_len = 0;
unsigned char passwd_len = 0;
char ssid[64] = {'\0'};
char passwd[64] = {'\0'};
bool ssid_updated = false;
bool passwd_updated = false;

namespace
{
    using namespace PLEN2;

    /*!
        Core instances
    */
    JointController  joint_ctrl;
    MotionController motion_ctrl(joint_ctrl);
    Interpreter      interpreter(motion_ctrl);

#if ENSOUL_PLEN2
    AccelerationGyroSensor sensor;
    Soul                   soul(sensor, motion_ctrl);
#endif

    /*!
        The application instance
    */
    class Application : public Protocol
    {
    private:
        static void (Application::*CONTROLLER_EVENT_HANDLER[])();
        static void (Application::*INTERPRETER_EVENT_HANDLER[])();
        static void (Application::*SETTER_EVENT_HANDLER[])();
        static void (Application::*GETTER_EVENT_HANDLER[])();

        static void (Application::**EVENT_HANDLER[])();

        Motion::Header    m_header_tmp;
        Motion::Frame     m_frame_tmp;
        Interpreter::Code m_code_tmp;

        void applyDiff()
        {
#if DEBUG_LESS
            volatile Utility::Profiler p(F("Application::applyDiff()"));

            System::debugSerial().print(F(">>> joint_id : "));
            System::debugSerial().println(Utility::hexbytes2uint(m_buffer.data, 2));

            System::debugSerial().print(F(">>> angle_diff : "));
            System::debugSerial().println(Utility::hexbytes2int(m_buffer.data + 2, 3));
#endif

            joint_ctrl.setAngleDiff(
                Utility::hexbytes2uint(m_buffer.data, 2),
                Utility::hexbytes2int(m_buffer.data + 2, 3)
            );
        }

        void apply()
        {
#if DEBUG_LESS
            volatile Utility::Profiler p(F("Application::apply()"));

            System::debugSerial().print(F(">>> joint_id : "));
            System::debugSerial().println(Utility::hexbytes2uint(m_buffer.data, 2));

            System::debugSerial().print(F(">>> angle : "));
            System::debugSerial().println(Utility::hexbytes2int(m_buffer.data + 2, 3));
#endif

            joint_ctrl.setAngle(
                Utility::hexbytes2uint(m_buffer.data, 2),
                Utility::hexbytes2int(m_buffer.data + 2, 3)
            );
        }

        void homePosition()
        {
#if DEBUG_LESS
            volatile Utility::Profiler p(F("Application::homePosition()"));
#endif

            joint_ctrl.loadSettings();
        }

        void playMotion()
        {
#if DEBUG_LESS
            volatile Utility::Profiler p(F("Application::playMotion()"));

            System::debugSerial().print(F(">>> slot : "));
            System::debugSerial().println(Utility::hexbytes2uint(m_buffer.data, 2));
#endif

            motion_ctrl.play(
                Utility::hexbytes2uint(m_buffer.data, 2)
            );
        }

        void stopMotion()
        {
#if DEBUG_LESS
            volatile Utility::Profiler p(F("Application::stopMotion()"));
#endif

            motion_ctrl.willStop();
        }

        void popCode()
        {
#if DEBUG_LESS
            volatile Utility::Profiler p(F("Application::popCode()"));
#endif

            interpreter.popCode();
        }

        void pushCode()
        {
#if DEBUG_LESS
            volatile Utility::Profiler p(F("Application::pushCode()"));

            System::debugSerial().print(F(">>> slot : "));
            System::debugSerial().println(Utility::hexbytes2uint(m_buffer.data, 2));

            System::debugSerial().print(F(">>> loop_count : "));
            System::debugSerial().println(Utility::hexbytes2uint(m_buffer.data + 2, 2));
#endif

            m_code_tmp.slot       = Utility::hexbytes2uint(m_buffer.data, 2);
            m_code_tmp.loop_count = Utility::hexbytes2uint(m_buffer.data + 2, 2) - 1;

            interpreter.pushCode(m_code_tmp);
        }

        void resetInterpreter()
        {
#if DEBUG_LESS
            volatile Utility::Profiler p(F("Application::resetInterpreter()"));
#endif

            interpreter.reset();
        }

        void setHome()
        {
#if DEBUG_LESS
            volatile Utility::Profiler p(F("Application::setHome()"));

            System::debugSerial().print(F(">>> joint_id : "));
            System::debugSerial().println(Utility::hexbytes2uint(m_buffer.data, 2));

            System::debugSerial().print(F(">>> angle : "));
            System::debugSerial().println(Utility::hexbytes2int(m_buffer.data + 2, 3));
#endif

            joint_ctrl.setHomeAngle(
                Utility::hexbytes2uint(m_buffer.data, 2),
                Utility::hexbytes2int(m_buffer.data + 2, 3)
            );
#if DEBUG_LESS
            System::debugSerial().println(F(">>> End Set Home : "));
#endif
        }

        void setJointSettings()
        {
#if DEBUG_LESS
            volatile Utility::Profiler p(F("Application::setJointSettings()"));
#endif

            joint_ctrl.resetSettings();
        }

        void setMax()
        {
#if DEBUG_LESS
            volatile Utility::Profiler p(F("Application::setMax()"));

            System::debugSerial().print(F(">>> joint_id : "));
            System::debugSerial().println(Utility::hexbytes2uint(m_buffer.data, 2));

            System::debugSerial().print(F(">>> angle : "));
            System::debugSerial().println(Utility::hexbytes2int(m_buffer.data + 2, 3));
#endif

            joint_ctrl.setMaxAngle(
                Utility::hexbytes2uint(m_buffer.data, 2),
                Utility::hexbytes2int(m_buffer.data + 2, 3)
            );
        }

        void setMotionFrame()
        {
#if DEBUG_LESS
            volatile Utility::Profiler p(F("Application::setMotionFrame()"));

            System::debugSerial().print(F(">>> slot : "));
            System::debugSerial().println(Utility::hexbytes2uint(m_buffer.data, 2));

            System::debugSerial().print(F(">>> frame_id : "));
            System::debugSerial().println(Utility::hexbytes2uint(m_buffer.data + 2, 2));

            System::debugSerial().print(F(">>> transition_time_ms : "));
            System::debugSerial().println(Utility::hexbytes2uint(m_buffer.data + 4, 4));

            for (int device_id = 0; device_id < JointController::SUM; device_id++)
            {
                System::debugSerial().print(F(">>> output["));
                System::debugSerial().print(device_id);
                System::debugSerial().print(F("] : "));
                System::debugSerial().println(Utility::hexbytes2int(m_buffer.data + 8 + device_id * 4, 4));
            }
#endif

            m_frame_tmp.transition_time_ms = Utility::hexbytes2uint(m_buffer.data + 4, 4);

            for (char device_id = 0; device_id < JointController::SUM; device_id++)
            {
                m_frame_tmp.joint_angle[device_id] = Utility::hexbytes2int(m_buffer.data + 8 + device_id * 4, 4);
            }

            if (m_installing)
            {
                if (m_frame_tmp.index < m_header_tmp.frame_length)
                {
                    m_frame_tmp.set(m_header_tmp.slot);
                    m_frame_tmp.index++;
                }

                if (m_frame_tmp.index == m_header_tmp.frame_length)
                {
                    m_installing = false;
                }
                else
                {
                    readByte('>');
                    accept();
                    transitState();

                    readByte('m');
                    readByte('f');
                    accept();
                    transitState();

                    readByte('0'); // dummy
                    readByte('0'); // dummy
                    readByte('0'); // dummy
                    readByte('0'); // dummy
                }
            }
            else
            {
                m_frame_tmp.index = Utility::hexbytes2uint(m_buffer.data + 2, 2);
                m_frame_tmp.set(Utility::hexbytes2uint(m_buffer.data, 2));
            }
        }

        void setMotionHeader()
        {
            strncpy(m_header_tmp.name, m_buffer.data + 2, 20);
            m_header_tmp.name[20] = '\0';
            m_buffer.data[2]      = '\0';

            if (   !(m_parser[ARGUMENTS_INCOMING]->parse(m_buffer.data))
                   || !(m_parser[ARGUMENTS_INCOMING]->parse(m_buffer.data + 22)) )
            {
                return;
            }

#if DEBUG_LESS
            volatile Utility::Profiler p(F("Application::setMotionHeader()"));

            System::debugSerial().print(F(">>> slot : "));
            System::debugSerial().println(Utility::hexbytes2uint(m_buffer.data, 2));

            System::debugSerial().print(F(">>> name : "));
            System::debugSerial().println(m_header_tmp.name);

            System::debugSerial().print(F(">>> func : "));
            System::debugSerial().println(Utility::hexbytes2uint(m_buffer.data + 22, 2));

            System::debugSerial().print(F(">>> arg0 : "));
            System::debugSerial().println(Utility::hexbytes2uint(m_buffer.data + 24, 2));

            System::debugSerial().print(F(">>> arg1 : "));
            System::debugSerial().println(Utility::hexbytes2uint(m_buffer.data + 26, 2));

            System::debugSerial().print(F(">>> frame_length : "));
            System::debugSerial().println(Utility::hexbytes2uint(m_buffer.data + 28, 2));
#endif

            m_header_tmp.slot         = Utility::hexbytes2uint(m_buffer.data, 2);
            m_header_tmp.frame_length = Utility::hexbytes2uint(m_buffer.data + 28, 2);

            switch (Utility::hexbytes2uint(m_buffer.data + 22, 2))
            {
                case 0:
                {
                    m_header_tmp.use_loop = 0;
                    m_header_tmp.use_jump = 0;

                    break;
                }

                case 1:
                {
                    m_header_tmp.use_loop   = 1;
                    m_header_tmp.use_jump   = 0;
                    m_header_tmp.loop_begin = Utility::hexbytes2uint(m_buffer.data + 24, 2);
                    m_header_tmp.loop_end   = Utility::hexbytes2uint(m_buffer.data + 26, 2);

                    break;
                }

                case 2:
                {
                    m_header_tmp.use_loop  = 0;
                    m_header_tmp.use_jump  = 1;
                    m_header_tmp.jump_slot = Utility::hexbytes2uint(m_buffer.data + 24, 2);

                    break;
                }
            }

            m_header_tmp.set();

            if (m_installing == true)
            {
                readByte('>');
                accept();
                transitState();

                readByte('m');
                readByte('f');
                accept();
                transitState();

                readByte('0'); // dummy
                readByte('0'); // dummy
                readByte('0'); // dummy
                readByte('0'); // dummy

                m_frame_tmp.index = 0;
            }
        }

        void setMin()
        {
#if DEBUG_LESS
            volatile Utility::Profiler p(F("Application::setMin()"));

            System::debugSerial().print(F(">>> joint_id : "));
            System::debugSerial().println(Utility::hexbytes2uint(m_buffer.data, 2));

            System::debugSerial().print(F(">>> angle : "));
            System::debugSerial().println(Utility::hexbytes2int(m_buffer.data + 2, 3));
#endif

            joint_ctrl.setMinAngle(
                Utility::hexbytes2uint(m_buffer.data, 2),
                Utility::hexbytes2int(m_buffer.data + 2, 3)
            );
        }

        void setWifi()
        {
        #if DEBUG_LESS
            volatile Utility::Profiler p(F("Application::setWifi()"));
        #endif
            if (!ssid_updated || !passwd_updated)
            {
            #if DEBUG
                System::debugSerial().print(ssid_updated);
                System::debugSerial().print(":");
                System::debugSerial().println(passwd_updated);
                System::debugSerial().print(m_buffer.data);
            #endif
                ssid_len = Utility::hexbytes2uint(m_buffer.data, 2);
                ssid_len = ssid_len > 64 ? 64 : ssid_len;
                passwd_len = Utility::hexbytes2uint(m_buffer.data + 2, 2);
                passwd_len = passwd_len > 64 ? 64 : passwd_len;
                memset(ssid, '\0', sizeof(ssid));
                memset(passwd, '\0', sizeof(passwd));
                if (passwd_len == 0)
                {
                    passwd_updated = true;
                }
            #if DEBUG
                System::debugSerial().print(F(">>> ssid len : "));
                System::debugSerial().println(Utility::hexbytes2uint(m_buffer.data, 2));

                System::debugSerial().print(F(">>> passwd len : "));
                System::debugSerial().println(Utility::hexbytes2int(m_buffer.data + 2, 2));
            #endif
            }
        }
        
        void setWifiSsid()
        {
        #if DEBUG_LESS
            volatile Utility::Profiler p(F("Application::setWifiSsid()"));
        #endif
            if (ssid_len)
            {
            #if DEBUG
                System::debugSerial().print(F(">>> ssid: "));
                System::debugSerial().println(m_buffer.data);
            #endif
                for (int i = 0; i < ssid_len; i++)
                {
                    ssid[i] = m_buffer.data[i];
                }
                System::debugSerial().println(ssid);
                ssid_updated = true;
                ssid_len = 0;
            }
        }

        void setWifiPassword()
        {
        #if DEBUG_LESS
            volatile Utility::Profiler p(F("Application::setWifiPassword()"));
        #endif
            if (passwd_len)
            {
            #if DEBUG
                System::debugSerial().print(F(">>> passwd: "));
                System::debugSerial().println(m_buffer.data);
            #endif
                for (int i = 0; i < passwd_len; i++)
                {
                    passwd[i] = m_buffer.data[i];
                }
                System::debugSerial().println(passwd);
                passwd_len = 0;
                passwd_updated = true;
            }
        }
        
        void getJointSettings()
        {
#if DEBUG_LESS
            volatile Utility::Profiler p(F("Application::getJointSettings()"));
#endif

            joint_ctrl.dump();
        }

        void getMotion()
        {
#if DEBUG_LESS
            volatile Utility::Profiler p(F("Application::getMotion()"));

            System::debugSerial().print(F(">>> slot : "));
            System::debugSerial().println(Utility::hexbytes2uint(m_buffer.data, 2));
#endif

            motion_ctrl.dump(
                Utility::hexbytes2uint(m_buffer.data, 2)
            );
        }

        void getVersionInformation()
        {
#if DEBUG_LESS
            volatile Utility::Profiler p(F("Application::getVersionInformation()"));
#endif

            System::dump();
        }
    public:
        virtual void afterHook()
        {
#if DEBUG
            volatile Utility::Profiler p(F("Application::afterFook()"));
#endif

            if (m_state == HEADER_INCOMING)
            {
                unsigned char header_id = m_parser[HEADER_INCOMING ]->index();
                unsigned char cmd_id    = m_parser[COMMAND_INCOMING]->index();

                (this->*EVENT_HANDLER[header_id][cmd_id])();

#if ENSOUL_PLEN2
                soul.userActionInputed();
#endif
            }
        }
    };

    void (Application::*Application::CONTROLLER_EVENT_HANDLER[])() =
    {
        &Application::applyDiff,
        &Application::apply,
        &Application::homePosition,
        &Application::playMotion,
        &Application::stopMotion,
        &Application::playMotion,
        &Application::stopMotion
    };

    void (Application::*Application::INTERPRETER_EVENT_HANDLER[])() =
    {
        &Application::popCode,
        &Application::pushCode,
        &Application::resetInterpreter
    };

    void (Application::*Application::SETTER_EVENT_HANDLER[])() =
    {
        &Application::setHome,
        &Application::setMotionHeader, // sanity check.
        &Application::setJointSettings,
        &Application::setMax,
        &Application::setMotionFrame,
        &Application::setMotionHeader,
        &Application::setMin,
        &Application::setWifiPassword,        
        &Application::setWifiSsid,
        &Application::setWifi,
    };

    void (Application::*Application::GETTER_EVENT_HANDLER[])() =
    {
        &Application::getJointSettings,
        &Application::getMotion,
        &Application::getVersionInformation
    };

    void (Application::**Application::EVENT_HANDLER[])() =
    {
        Application::CONTROLLER_EVENT_HANDLER,
        Application::INTERPRETER_EVENT_HANDLER,
        Application::SETTER_EVENT_HANDLER,
        Application::GETTER_EVENT_HANDLER
    };

    Application app;
}


/*!
    @brief Setup

    Put your setup code here, to run once:

    @attention
    Digital pin's output is an indefinite if you don't give an initialize value.
    Please ensure that setup the pins which are configurable.
*/
void setup()
{
    volatile PLEN2::System system;
    ExternalFs::init();

    joint_ctrl.Init();
    joint_ctrl.loadSettings();
    System::setup_smartconfig();

#if ENSOUL_PLEN2
    /*!
      @attention
      The order of power supplied or firmware startup timing is base-board, head-board.
      If the sampling method calls from early timing, program freezes because synchronism of communication is missed.
      (Generally, it is going to success setup() inserts 3000[msec] delays.)
    */
    delay(3000);
#endif
}


/*!
    @brief Main polling loop

    Put your main code here, to run repeatedly:
*/
void loop()
{
    if (motion_ctrl.playing())
    {
        if (motion_ctrl.frameUpdatable())
        {
            motion_ctrl.updateFrame();
        }

        if (motion_ctrl.updatingFinished())
        {
            if (motion_ctrl.nextFrameLoadable())
            {
                motion_ctrl.loadNextFrame();
            }
            else
            {
                motion_ctrl.stop();

                if (interpreter.ready())
                {
                    interpreter.popCode();
                }
            }
        }
    }

    if (PLEN2::System::SystemSerial().available())
    {
        app.readByte(PLEN2::System::SystemSerial().read());

        if (app.accept())
        {
            app.transitState();

        }
    }
    if (PLEN2::System::tcp_available())
    {
        app.readByte(PLEN2::System::tcp_read());
        if (app.accept())
        {
            app.transitState();
        }
    }
    PLEN2::System::handleClient();
#if ENSOUL_PLEN2
    soul.log();
    soul.action();
#endif
}

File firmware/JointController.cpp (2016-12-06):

/*
    Copyright (c) 2015,
    - Kazuyuki TAKASE - https://github.com/junbowu
    - PLEN Project Company Inc. - https://plen.jp

    This software is released under the MIT License.
    (See also : http://opensource.org/licenses/mit-license.php)
*/
#include "Arduino.h"
#include <Wire.h>
#include <Servo.h>
#include <Ticker.h>
#include <Adafruit_PWMServoDriver.h>

#include "Pin.h"
#include "Profiler.h"
#include "System.h"
#include "JointController.h"
#include "ExternalFs.h"
#include "Motion.h"

Adafruit_PWMServoDriver pwm;
Servo GPIO12SERVO;
Servo GPIO14SERVO;
Servo EyeOut;
Ticker flipper;
Ticker flipper_second;

extern File fp_config;
/*!
    @note
    If you want to apply the firmware to PLEN1.4, set the macro to false.
*/
#define PLEN2_JOINTCONTROLLER_PWM_OUT_00_07_REGISTER OCR1C
#define PLEN2_JOINTCONTROLLER_PWM_OUT_08_15_REGISTER OCR1B
#define PLEN2_JOINTCONTROLLER_PWM_OUT_16_23_REGISTER OCR1A

volatile bool PLEN2::JointController::m_1cycle_finished = false;
int PLEN2::JointController::m_pwms[PLEN2::JointController::SUM];

//eyes control
int _enable;
int _eye_count_step;
int _eye_count;

namespace
{
    namespace Shared
    {
        using namespace PLEN2;

        PROGMEM const int m_SETTINGS_INITIAL[] =
        {
            JointController::ANGLE_MIN, JointController::ANGLE_MAX,  0, // [01] Left : Shoulder Pitch
            JointController::ANGLE_MIN, JointController::ANGLE_MAX,  150, // [02] Left : Thigh Yaw
            JointController::ANGLE_MIN, JointController::ANGLE_MAX,  350, // [03] Left : Shoulder Roll
            JointController::ANGLE_MIN, JointController::ANGLE_MAX, -100, // [04] Left : Elbow Roll
            JointController::ANGLE_MIN, JointController::ANGLE_MAX, -100, // [05] Left : Thigh Roll
            JointController::ANGLE_MIN, JointController::ANGLE_MAX,  -50, // [06] Left : Thigh Pitch
            JointController::ANGLE_MIN, JointController::ANGLE_MAX,  500, // [07] Left : Knee Pitch
            JointController::ANGLE_MIN, JointController::ANGLE_MAX,  300, // [08] Left : Foot Pitch
            JointController::ANGLE_MIN, JointController::ANGLE_MAX,  -50, // [09] Left : Foot Roll
            JointController::ANGLE_MIN, JointController::ANGLE_MAX, JointController::ANGLE_NEUTRAL,
            JointController::ANGLE_MIN, JointController::ANGLE_MAX, JointController::ANGLE_NEUTRAL,
            JointController::ANGLE_MIN, JointController::ANGLE_MAX, JointController::ANGLE_NEUTRAL,
            JointController::ANGLE_MIN, JointController::ANGLE_MAX,   0, // [10] Right : Shoulder Pitch
            JointController::ANGLE_MIN, JointController::ANGLE_MAX, -150, // [11] Right : Thigh Yaw
            JointController::ANGLE_MIN, JointController::ANGLE_MAX, -350, // [12] Right : Shoulder Roll
            JointController::ANGLE_MIN, JointController::ANGLE_MAX,  100, // [13] Right : Elbow Roll
            JointController::ANGLE_MIN, JointController::ANGLE_MAX,  100, // [14] Right : Thigh Roll
            JointController::ANGLE_MIN, JointController::ANGLE_MAX,   50, // [15] Right : Thigh Pitch
            JointController::ANGLE_MIN, JointController::ANGLE_MAX, -500, // [16] Right : Knee Pitch
            JointController::ANGLE_MIN, JointController::ANGLE_MAX, -300, // [17] Right : Foot Pitch
            JointController::ANGLE_MIN, JointController::ANGLE_MAX,   50, // [18] Right : Foot Roll
            JointController::ANGLE_MIN, JointController::ANGLE_MAX, JointController::ANGLE_NEUTRAL,
            JointController::ANGLE_MIN, JointController::ANGLE_MAX, JointController::ANGLE_NEUTRAL,
            JointController::ANGLE_MIN, JointController::ANGLE_MAX, JointController::ANGLE_NEUTRAL
        };

        const int ERROR_LVALUE = -32768;
    }
}


void PLEN2::JointController::Init()
{
    pwm = Adafruit_PWMServoDriver();

    pinMode(Pin::PCA9685_ENABLE(), OUTPUT);
    digitalWrite(Pin::PCA9685_ENABLE(), LOW);

    // Software PWM PIN
    GPIO12SERVO.attach(Pin::PWM_OUT_12());
    GPIO14SERVO.attach(Pin::PWM_OUT_14());

    _enable = false;
    _eye_count = 100;
    EyeOut.attach(Pin::LED_OUT(), 200, 20000);

    pinMode(Pin::PCA9685_ENABLE(), OUTPUT);
    digitalWrite(Pin::PCA9685_ENABLE(), LOW);

    // Initialize I2C
    Wire.begin(4, 5);

    // PWMServoDriver
    pwm.begin();
    pwm.setPWMFreq(PWM_FREQ());   // servos run at 300Hz updates

    delay(500);

    for (char joint_id = 0; joint_id < SUM; joint_id++)
    {
        m_SETTINGS[joint_id].MIN  = Shared::m_SETTINGS_INITIAL[joint_id * 3];
        m_SETTINGS[joint_id].MAX  = Shared::m_SETTINGS_INITIAL[joint_id * 3 + 1];
        m_SETTINGS[joint_id].HOME = Shared::m_SETTINGS_INITIAL[joint_id * 3 + 2];
        setAngle(joint_id, m_SETTINGS[joint_id].HOME);
    }
}
PLEN2::JointController::JointController()
{

}


void PLEN2::JointController::loadSettings()
{
#if DEBUG
    volatile Utility::Profiler p(F("JointController::loadSettings()"));
#endif

    unsigned char* filler = reinterpret_cast<unsigned char*>(m_SETTINGS);

    if (ExternalFs::readByte(INIT_FLAG_ADDRESS(), fp_config) != INIT_FLAG_VALUE())
    {
        ExternalFs::writeByte(INIT_FLAG_ADDRESS(), INIT_FLAG_VALUE(), fp_config);
        ExternalFs::write(SETTINGS_HEAD_ADDRESS(), sizeof(m_SETTINGS), filler, fp_config);
        System::debugSerial().println(F("reset config\n"));
    }
    else
    {
        ExternalFs::read(SETTINGS_HEAD_ADDRESS(), sizeof(m_SETTINGS), filler, fp_config);
        System::debugSerial().println(F("read config"));
    }

    for (char joint_id = 0; joint_id < SUM; joint_id++)
    {
        setAngle(joint_id, m_SETTINGS[joint_id].HOME);
    }

    flipper.attach_ms(Motion::Frame::UPDATE_INTERVAL_MS, PLEN2::JointController::updateAngle);
    flipper_second.attach(1, PLEN2::JointController::updateEyes);
}


void PLEN2::JointController::resetSettings()
{
#if DEBUG
    volatile Utility::Profiler p(F("JointController::resetSettings()"));
#endif

    ExternalFs::writeByte(INIT_FLAG_ADDRESS(), INIT_FLAG_VALUE(), fp_config);

    for (char joint_id = 0; joint_id < SUM; joint_id++)
    {
        m_SETTINGS[joint_id].MIN  = Shared::m_SETTINGS_INITIAL[joint_id * 3];
        m_SETTINGS[joint_id].MAX  = Shared::m_SETTINGS_INITIAL[joint_id * 3 + 1];
        m_SETTINGS[joint_id].HOME = Shared::m_SETTINGS_INITIAL[joint_id * 3 + 2];

        setAngle(joint_id, m_SETTINGS[joint_id].HOME);
    }

    ExternalFs::write(SETTINGS_HEAD_ADDRESS(), sizeof(m_SETTINGS),
                      reinterpret_cast<const unsigned char*>(m_SETTINGS), fp_config);
}


const int& PLEN2::JointController::getMinAngle(unsigned char joint_id)
{
#if DEBUG
    volatile Utility::Profiler p(F("JointController::getMinAngle()"));
#endif

    if (joint_id >= SUM)
    {
#if DEBUG
        System::debugSerial().print(F(">>> bad argment! : joint_id = "));
        System::debugSerial().println(static_cast<int>(joint_id));
#endif

        return Shared::ERROR_LVALUE;
    }

    return m_SETTINGS[joint_id].MIN;
}
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

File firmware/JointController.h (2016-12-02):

/*!
    @file      JointController.h
    @brief     Management class of joints.
    @author    Kazuyuki TAKASE
    @copyright The MIT License - http://opensource.org/licenses/mit-license.php
*/

#ifndef PLEN2_JOINT_CONTROLLER_H
#define PLEN2_JOINT_CONTROLLER_H

#define USE_DIGTAL_SERVO 0
#define MAX_SERVOS 24
namespace PLEN2
{
    class JointController;
}

/*!
    @brief Management class of joints

    In Atmega32u4, one timer can output 3 PWM signals at a time.
    The MCU can control 24 servos by connecting 3bit multiplexer in each signal output lines.

    @note
    There is information about PLEN1.4's configuration below.
    @code
    enum {
        SUM = 24, //!< Summation of the servos controllable.

        ANGLE_MIN     = -600, //!< Min angle of the servos.
        ANGLE_MAX     =  600, //!< Max angle of the servos.
        ANGLE_NEUTRAL =    0  //!< Neutral angle of the servos.
    };

    //! @brief PWM width that to make min angle
    inline static const int PWM_MIN()     { return 492;  }

    //! @brief PWM width that to make max angle
    inline static const int PWM_MAX()     { return 816;  }

    //! @brief PWM width that to make neutral angle
    inline static const int PWM_NEUTRAL() { return 654;  }
    @endcode
*/
class PLEN2::JointController
{
public:
    enum
    {
        SUM = MAX_SERVOS, //!< Summation of the servos controllable.

        ANGLE_MIN     = -800, //!< Min angle of the servos.
        ANGLE_MAX     =  800, //!< Max angle of the servos.
        ANGLE_NEUTRAL =    0  //!< Neutral angle of the servos.
    };

private:
    //! @brief Initialized flag's address on internal EEPROM
    inline static const int INIT_FLAG_ADDRESS()
    {
        return 0;
    }

    //! @brief Initialized flag's value
    inline static const unsigned char INIT_FLAG_VALUE()
    {
        return 2;
    }

    //! @brief Head-address of joint settings on internal EEPROM
    inline static const int SETTINGS_HEAD_ADDRESS()
    {
        return 1;
    }

    /*!
        @brief Management class of joint setting
    */
    class JointSetting
    {
    public:
        int MIN;  //!< Setting about min angle.
        int MAX;  //!< Setting about max angle.
        int HOME; //!< Setting about home angle.

        /*!
            @brief Constructor
        */
        JointSetting()
            : MIN(ANGLE_MIN)
            , MAX(ANGLE_MAX)
            , HOME(ANGLE_NEUTRAL)
        {
            // noop.
        }
    };

    JointSetting m_SETTINGS[SUM];
public:
    /*!
        @brief Management class (as namespace) of multiplexer

        @note
        The methods the class has are more accurate that there are in the namespace named Multiplexer,
        but C++'s idiom doesn't accept syntax that described before.
    */
    class Multiplexer
    {
    public:
        //! @brief Summation of multiplexers
        inline static const int SUM()
        {
            return 3;
        }

        //! @brief Number of controllable lines by a multiplexer
        inline static const int SELECTABLE_LINES()
        {
            return 8;
        }
    };
#if USE_DIGTAL_SERVO
    inline static const int PWM_FREQ()
    {
        return 320;
    }

    //! @brief PWM width that to make min angle
    inline static const int PWM_MIN()
    {
        return 1100;
    }

    //! @brief PWM width that to make max angle
    inline static const int PWM_MAX()
    {
        return 2700;
    }

    //! @brief PWM width that to make neutral angle
    inline static const int PWM_NEUTRAL()
    {
        return 1900;
    }
#else
    inline static const int PWM_FREQ()
    {
        return 60;
    }

    //! @brief PWM width that to make min angle
    inline static const int PWM_MIN()
    {
        return 175;
    }

    //! @brief PWM width that to make max angle
    inline static const int PWM_MAX()
    {
        return 575;
    }

    //! @brief PWM width that to make neutral angle
    inline static const int PWM_NEUTRAL()
    {
        return 375;
    }
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

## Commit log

2016-08-31 update stl
2016-08-31 update hander
    [servo_assem_type1.STL, servo_bracket_elbow_2.STL]
2016-09-12 update ankle_2
    [servo_bracket_ankle_2.STL, servo_bracket_ankle_2_mirror.STL]
2016-10-05 update hand
    [hand.stl]
2016-10-12 add Circuit diagram
2016-10-26 update motion editor （fix slot miss）
2016-10-26 add power switch holder
    [power_switch_holder.STL]
2016-11-14 add skate stl,enjoy it!
    [skate_base.stl, skate_wheel_seats.stl]
2016-11-14 add pl2303 driver
2016-11-23 update stl & firmware
    [servo_assem_type2.STL, servo_assem_type2_mirror.STL, servo_type_part1.STL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]
2016-12-05 update 3D Model
    [BARB.STL, HEAD.STL, barb.STL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]
2016-12-18 added assembly instructions
